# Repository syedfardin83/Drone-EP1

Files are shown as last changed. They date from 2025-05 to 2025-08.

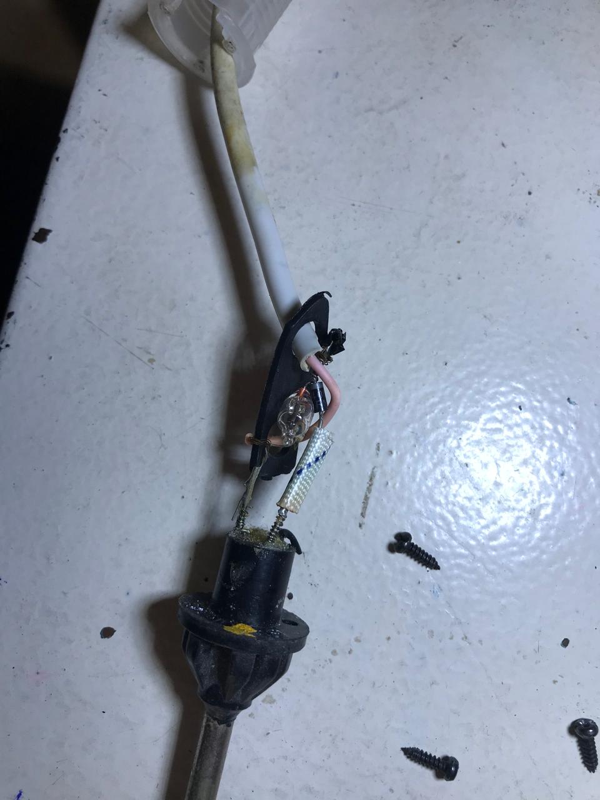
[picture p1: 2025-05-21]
Images/solder gun.jpg

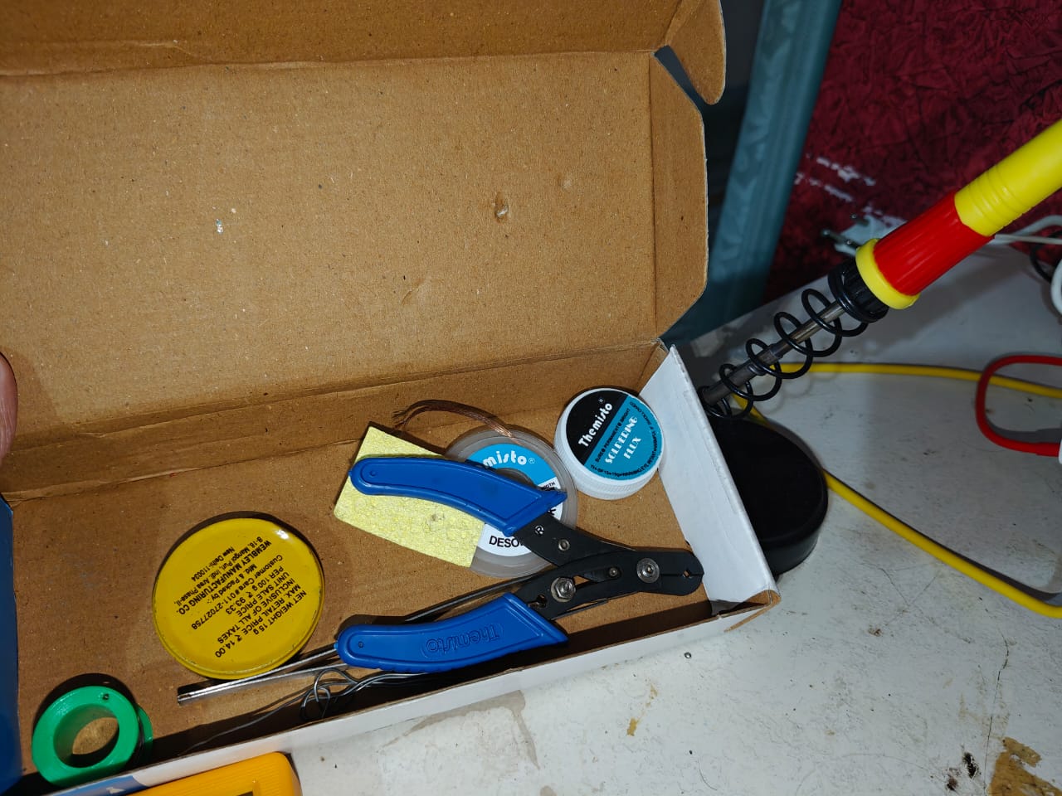
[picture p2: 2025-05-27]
Images/Soldering set.jpg

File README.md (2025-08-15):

##  LOS (Lark OS):
LOS is a firmware specifically built for the drone flight controller Lark1.

It inludes:
- Reading desired angles/rates from the in-built bluetooth on the ESP32.
- Reading the IMU data (MPU6050).
- Using a complementary filter to obtain the current angles of the drone.
- A PID loop to maintain stability and a smooth flight.

### LOS 1.0
A super loop firmware, with only 1dof control (throttle coontrol only). It was built to test basic tasks like Bluetooth reading, commands string formatting, and motor PWM outputs. It does not include IMU reading and PID calculations.

It is tested and works well.

### LOS 1.1
It was supposed to be complete functional drone superloop firmware with 6dof. But, it did not function, due to some superloop firmware complications.

It is tested and does not work. Hence, moving on to LOS2 which will be FreeRTOS based.

### LOS 2.0
It is a FreeRTOS based complete drone firmware. It has two tasks.
- BT read task
- MPU read + PID calculation

As the Bluetooth task was in the same task in LOS1.1, it was causing the major lag, hence LOS2.0 separates the BT task, while the rest of the tasks are together in another task.

### LOS 2.1
It is an improverment over the LOS 2.0, which now includes 4 tasks.
- BT reading
- IMU reading
- Angles calculation - Complementary filter
- PID loop

LOS 2.1 is more robust, as it uses queues for intertransmission of data between tasks.

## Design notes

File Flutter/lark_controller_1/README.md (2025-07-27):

# lark_controller_1

A new Flutter project.

## Getting Started

This project is a starting point for a Flutter application.

A few resources to get you started if this is your first Flutter project:

- [Lab: Write your first Flutter app](https://docs.flutter.dev/get-started/codelab)
- [Cookbook: Useful Flutter samples](https://docs.flutter.dev/cookbook)

For help getting started with Flutter development, view the
[online documentation](https://docs.flutter.dev/), which offers tutorials,
samples, guidance on mobile development, and a full API reference.

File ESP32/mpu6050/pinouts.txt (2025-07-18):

MPU6050     ESP32

VCC	     3.3v
GND	     GND
SDA	     25
SCL	     26

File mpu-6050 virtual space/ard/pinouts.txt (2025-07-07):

MPU6050     Arduino Uno

VCC	     5V 
GND	     GND
SDA	     A4
SCL	     A5

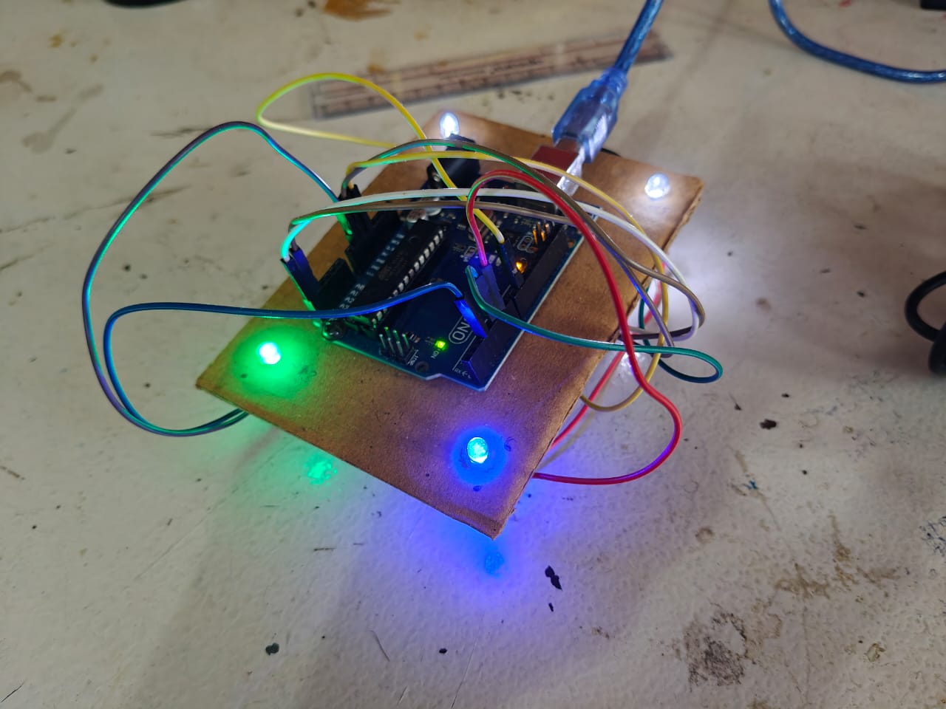
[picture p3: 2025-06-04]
Images/LED PID.jpeg

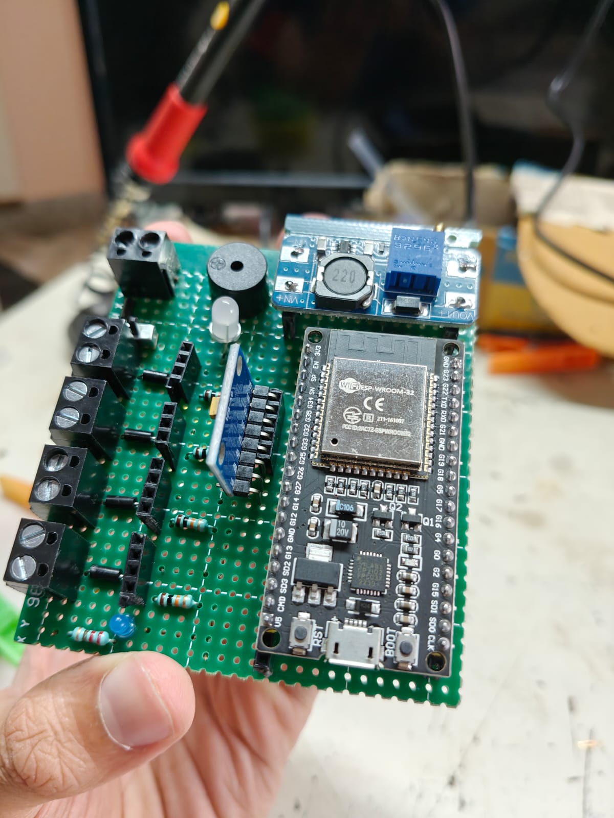
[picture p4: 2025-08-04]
Images/Lark1.jpeg

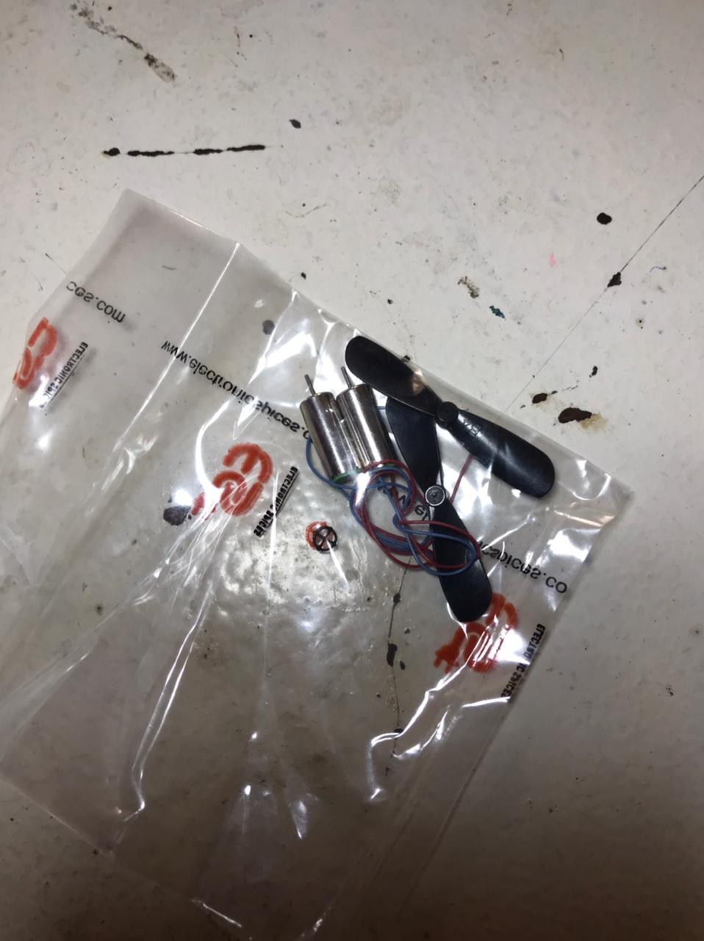
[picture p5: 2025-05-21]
Images/8520 Motors.jpg

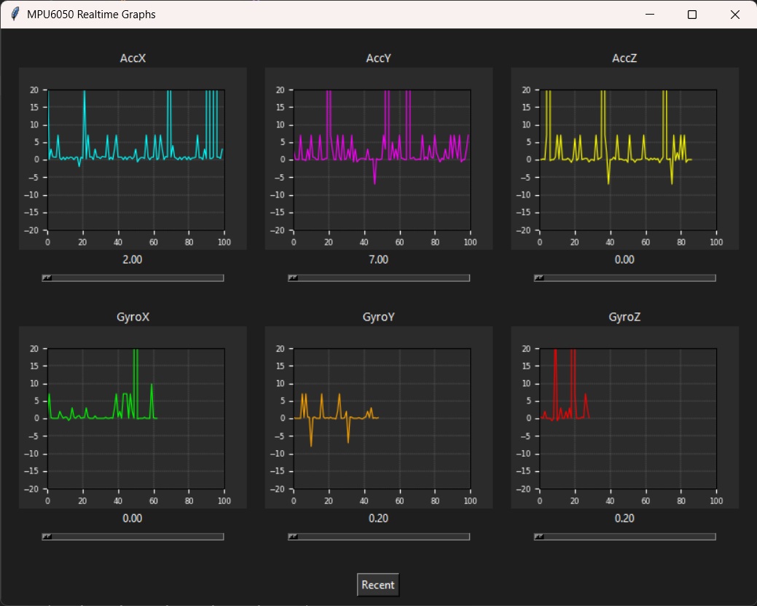
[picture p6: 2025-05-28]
Images/GUI 2.jpg

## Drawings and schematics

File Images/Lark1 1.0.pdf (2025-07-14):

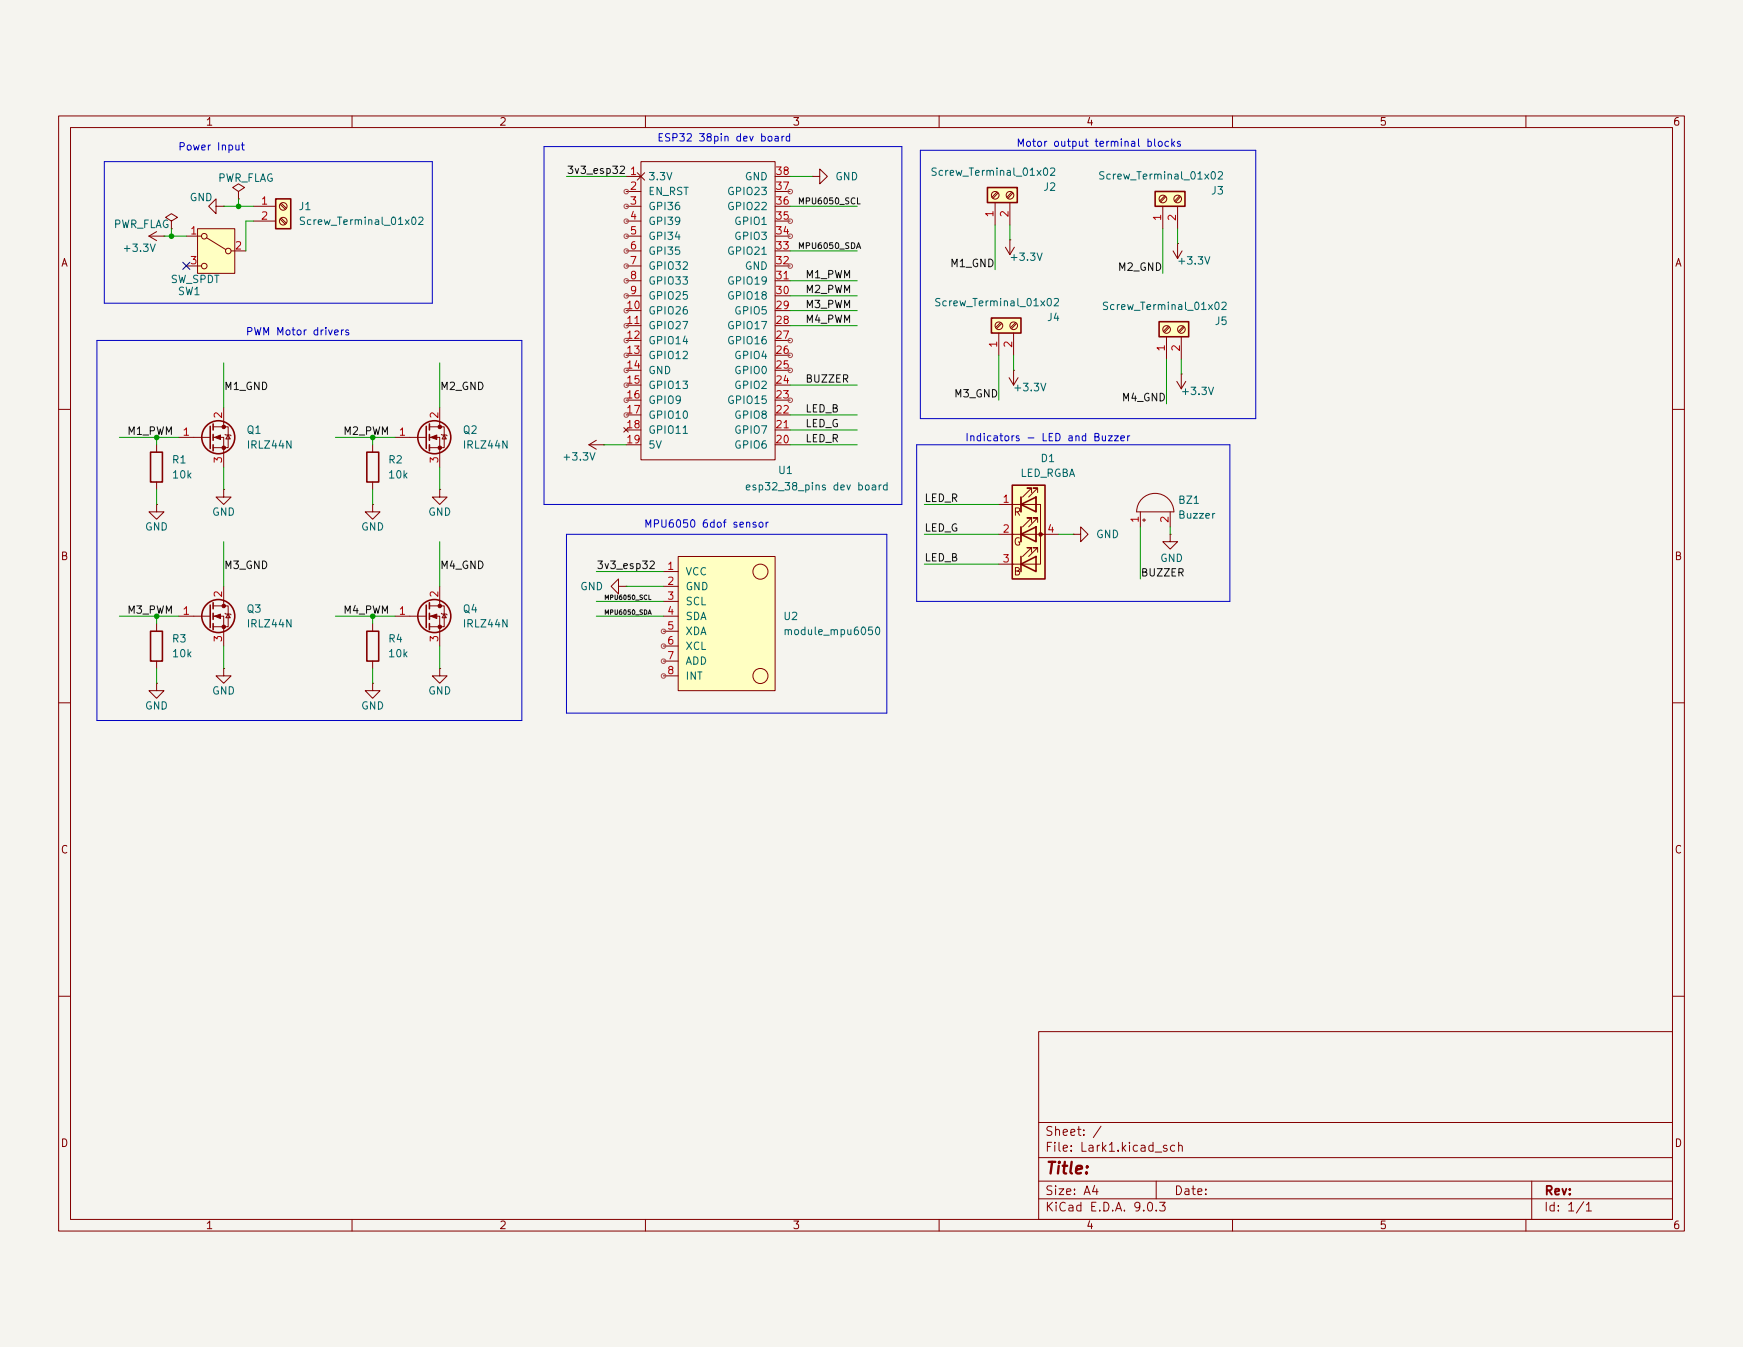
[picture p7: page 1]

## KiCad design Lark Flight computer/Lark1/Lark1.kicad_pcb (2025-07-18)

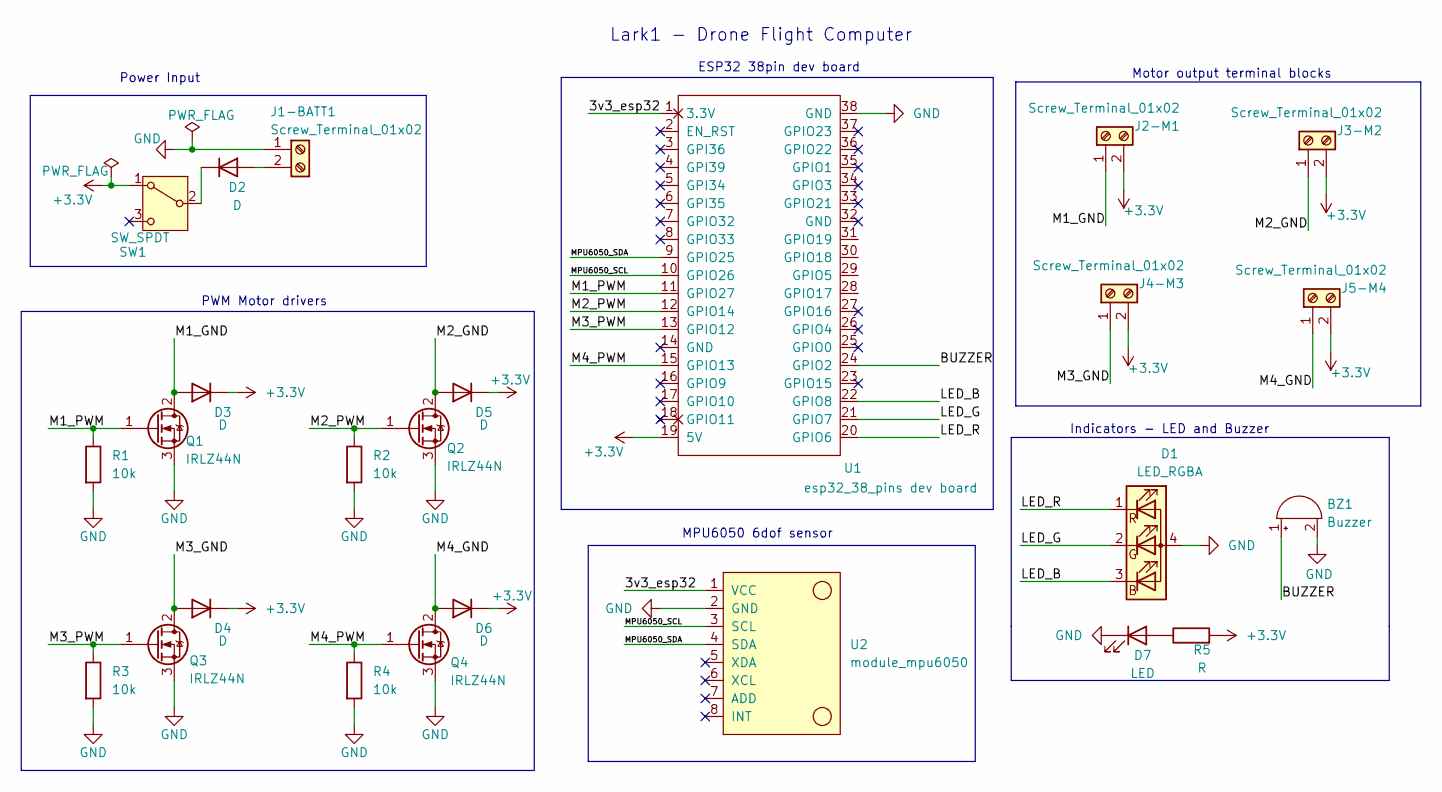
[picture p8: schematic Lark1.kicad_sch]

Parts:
BZ1: Buzzer; Buzzer_12x9.5RM7.6
D1: LED_RGBA; LED_D5.0mm-4_RGB_Wide_Pins
D2, D3, D4, D5, D6: D; D_5KPW_P12.70mm_Horizontal
D7: LED; LED_D3.0mm
J1-BATT1, J2-M1, J3-M2, J4-M3, J5-M4: Screw_Terminal_01x02; TerminalBlock_Altech_AK300-2_P5.00mm
Q1, Q2, Q3, Q4: IRLZ44N; TO-220-3_Vertical
R1, R2, R3, R4: 10k; R_Axial_DIN0204_L3.6mm_D1.6mm_P5.08mm_Horizontal
R5: R; R_Axial_DIN0204_L3.6mm_D1.6mm_P5.08mm_Horizontal
SW1: SW_SPDT; SW_Slide_SPDT_Angled_CK_OS102011MA1Q
U1: esp32_38_pins dev board; PinSocket_2x19_P2.54mm_Vertical
U2: module_mpu6050; PinSocket_1x08_P2.54mm_Vertical

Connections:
+3.3V: D3.1 (K), D4.1 (K), D5.1 (K), D6.1 (K), J2-M1.2, J3-M2.2, J4-M3.2, J5-M4.2, R5.2, SW1.1 (A), U1.19 (5V)
/3v3_esp32: U1.1 (3.3V), U2.1 (VCC)
/BUZZER: BZ1.1 (+), U1.24 (GPIO2)
/LED_B: D1.3 (BK), U1.22 (GPIO8)
/LED_G: D1.2 (GK), U1.21 (GPIO7)
/LED_R: D1.1 (RK), U1.20 (GPIO6)
/M1_GND: D3.2 (A), J2-M1.1, Q1.2 (D)
/M1_PWM: Q1.1 (G), R1.1, U1.11 (GPIO27)
/M2_GND: D5.2 (A), J3-M2.1, Q2.2 (D)
/M2_PWM: Q2.1 (G), R2.1, U1.12 (GPIO14)
/M3_GND: D4.2 (A), J4-M3.1, Q3.2 (D)
/M3_PWM: Q3.1 (G), R3.1, U1.13 (GPIO12)
/M4_GND: D6.2 (A), J5-M4.1, Q4.2 (D)
/M4_PWM: Q4.1 (G), R4.1, U1.15 (GPIO13)
/MPU6050_SCL: U1.10 (GPIO26), U2.3 (SCL)
/MPU6050_SDA: U1.9 (GPIO25), U2.4 (SDA)
GND: BZ1.2 (-), D1.4 (A), D7.1 (K), J1-BATT1.1, Q1.3 (S), Q2.3 (S), Q3.3 (S), Q4.3 (S), R1.2, R2.2, R3.2, R4.2, U1.38 (GND), U2.2 (GND)
unnamed: D2.2 (A), J1-BATT1.2
unnamed: D2.1 (K), SW1.2 (B)
unnamed: D7.2 (A), R5.1

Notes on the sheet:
Indicators - LED and Buzzer
PWM Motor drivers
Power Input
MPU6050 6dof sensor
Lark1 - Drone Flight Computer
ESP32 38pin dev board
Motor output terminal blocks

Board: 2 copper layers, 25 parts (0 on the bottom side), 20 nets, no tracks yet.

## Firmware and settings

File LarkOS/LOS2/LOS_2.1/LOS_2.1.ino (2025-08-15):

//LOS 2.0 - FreeRTOS Based 6dof, bluetooth controlled Lark Firmware
//Three main tasks
//1. Bluetooth Input
//2. MPU6050 Sensor input and processing
//3. PID

//  Axis mapping:
//  x-axis : yaw
//  y-axis : pitch
//  z-axis : roll 

//ToDO:
//vTaskDelay after every task
//Proper heap memory allocation for each task

//  Importing modules
#include "BluetoothSerial.h"
#include <math.h>
#include <Adafruit_MPU6050.h>
#include <Adafruit_Sensor.h>
#include <Wire.h>

//  Defining App CPU  
#if CONFIG_FREERTOS_UNICORE
static const int app_cpu = 0;
#else
static const int app_cpu = 1;
#endif

//  Software Objects
BluetoothSerial SerialBT;
Adafruit_MPU6050 mpu;

//  BT read variables
String inputString = "";
bool stringEnd = false;
char ch;

// Drone control variables
double desiredAngles[3] = {0,0,0}; ////////////////////////////
double throttleIncrement = 0;
double throttle = 0; //////////////////
double* offsets;
double integratedAngles[3] = {0,0,0};
double accAngles[3] = {0,0,0};
double compAngles[3] = {0,0,0};
double alpha = 0.98;

//MPU
#define SCL_PIN 17
#define SDA_PIN 26
double* mpu_data;////////////////////////////

// PID variables
double P=0.09,I=0.01,D=0.01;
double P_terms[3] = {0,0,0};
double I_terms[3] = {0,0,0};
double D_terms[3] = {0,0,0};
double current_errors[3] = {0,0,0};
double previous_errors[3] = {0,0,0};
double rate_outputs[3] = {0,0,0};

// Motor inputs
int motor_inputs[4] = {0,0,0,0};

// Time variables
double dt1;

#define bt_name "LOS 2.0"

//  FreeRTOS Queues
static QueueHandle_t desiredAnglesQ;
static uint8_t desiredAnglesQ_l = 3;

static QueueHandle_t throttleQ;
static uint8_t throttleQ_l = 3;

static QueueHandle_t mpu_dataQ;
static uint8_t mpu_dataQ_l = 3;

static QueueHandle_t dt1Q;
static uint8_t dt1Q_l = 3;

static QueueHandle_t current_anglesQ;
static uint8_t current_anglesQ_l = 3;


String* splitBySpace(String str){
  static String words[10];int i=0;String word = "";int wordIndex = 0;
  while(i<str.length()){
    if((str[i]==' ')){
      words[wordIndex] = word;
      word="";
      wordIndex++;i++;
      continue;
    }
    if(i==str.length()-1){
      word+=str[i];
      words[wordIndex] = word;break;
    }
    word+=str[i];
    i++;
  }
  return words;
}

double* getData(){
  /* Get new sensor events with the readings */
  sensors_event_t a, g, temp;
  mpu.getEvent(&a, &g, &temp);
  static double arr[6];
  arr[0] = a.acceleration.x;
  arr[1] = a.acceleration.y;
  arr[2] = a.acceleration.z;

  arr[3] = g.gyro.x;
  arr[4] = g.gyro.y;
  arr[5] = g.gyro.z;
  return arr;
  // AccX = a.acceleration.x
  // return [a.acceleration.x,a.acceleration.y,a.acceleration.z,a.gyro.x,a.gyro.y,a.gyro.z];
  // double data[6] = {a.acceleration.x, a.acceleration.y, a.acceleration.z, a.gyro.x, a.gyro.y, a.gyro.z};
}

double* getFilteredData(int n){
  double sums[6] = {0,0,0,0,0,0};

  static double avgs[6];

  //Finding sums
  for(int i=1; i<=n; i++){
    static double* data;
    data = getData();
    for(int j=0; j<6; j++){
      sums[j] = sums[j]+data[j];
    }
  }

  //Finding avgs
  for(int i=0; i<6; i++){
    avgs[i] = sums[i]/n;
  }

  return avgs;
}

double* calliberateSensor(){
  static double offsets[6];
  static double* data;
  data = getFilteredData(5);

  for(int i=0; i<6; i++){
    offsets[i] = data[i];
  }

  return offsets;
}

//  FreeRTOS Tasks
void BT_update_task(void *param){
  Serial.println("Entered the bluetooth task");
  int i;
  while(1){
    if(SerialBT.available()){
      ch = SerialBT.read();
      if(ch=='\n'){
        stringEnd = true;
        inputString.trim();
      }else{
        inputString+=ch;
      }
    }
    if(stringEnd){
      String* commands = splitBySpace(inputString);

      //Update desired angles
      for(i=0;i<3;i++){
        desiredAngles[i] = radians(commands[i].toDouble());
      }
      throttleIncrement = commands[3].toDouble();
      throttle+=(throttleIncrement*0.1);
      throttleIncrement = 0;

      //  Push to queue
      if(xQueueSend(desiredAnglesQ, desiredAngles,3) != pdTRUE){
        Serial.println("desiredAnglesQ full!");
      }

      if(xQueueSend(throttleQ, &throttle, 3) != pdTRUE){
        Serial.println("throttle Q full!");
      }

      inputString = "";
      stringEnd = false;
    }
    vTaskDelay(10/portTICK_PERIOD_MS);
  }
}

void mpu_read_pid_task(void *param){
  Serial.println("Entered MPU task");
  static TickType_t last_tick;
  static TickType_t curr_tick;
  int i;

  while(1){
    // prev_tick = xTaskGetTickCount();
    last_tick = xTaskGetTickCount();
    mpu_data = getFilteredData(5);
    curr_tick = xTaskGetTickCount();

    dt1 = ((curr_tick-last_tick)*portTICK_PERIOD_MS)/1000;
    
    //  Push To Queue
    if(xQueueSend(mpu_dataQ, mpu_data, 3) != pdTRUE){
      Serial.println("mpu_dataQ full!");
    }

    if(xQueueSend(dt1Q, &dt1, 3) != pdTRUE){
      Serial.println("dt1Q full!");
    }

    vTaskDelayUntil(&last_tick, 40/portTICK_PERIOD_MS);
  }
}

void calculate_angles_task(void *param){
  double dt1; double mpu_data_local[6];int i;
  while(1){
    //  Read Queues
    if(xQueueReceive(dt1Q,&dt1,3)!=pdTRUE){
      Serial.println("Failed to read dt1Q");
    }
    
    if(xQueueReceive(mpu_dataQ,&mpu_data_local,3) != pdTRUE){
      Serial.println("Failed to read mpu_dataQ");
    }

    //  Integrate Angles
    for(i=0;i<3;i++){
      integratedAngles[i]+=dt1*(mpu_data_local[i+3]-offsets[i+3]);
    }

    //  Acc angles
    accAngles[0] = -integratedAngles[0];
    if(mpu_data[0]==0){
      accAngles[1] = 3.14/2;
      accAngles[2] = 3.14/2;     
    }else{
      accAngles[1] = atan(mpu_data_local[2]/mpu_data_local[0]);
      accAngles[2] = atan(mpu_data_local[1]/mpu_data_local[0]);
    }

    //  Complementary filter
    for(i=0;i<3;i++){
      compAngles[i] = alpha*integratedAngles[i] + (1-alpha)*accAngles[i];
    }

    //  Update Queue
    if(xQueueSend(current_anglesQ,&compAngles,3)!=pdTRUE){
      Serial.println("current_anglesQ full!");
    }
  }
}

void pid_task(void *param){
  double current_angles[3]; double desired_angles_loacal[3]; double throttle_local;
  static TickType_t last_tick;
  static TickType_t curr_tick;
  double dt2;
  while(1){
    //  Read Queues
    if(xQueueReceive(current_anglesQ,&current_angles,3)!=pdTRUE){
      Serial.println("Failed to read current_anglesQ");
    }

    if(xQueueReceive(desiredAnglesQ,&desired_angles_loacal,3)!=pdTRUE){
      Serial.println("Failed to read desiredAnglesQ");
    }

    if(xQueueReceive(throttleQ,&throttle_local,3)!=pdTRUE){
      Serial.println("Failed to read throttleQ");
    }

    //Find errors
    prev_tick = xTaskGetTickCount();
    for(i=0;i<3;i++){
      current_errors[i] = current_angles[i]-desired_angles_loacal[i];
    }
    curr_tick = xTaskGetTickCount();
    dt2 = ((curr_tick-last_tick)*portTICK_PERIOD_MS)/1000;


    //Find rate outputs
    //****************** dt not properly calculated *****************************
    for(i=0;i<3;i++){
      P_terms[i] = P*current_errors[i];
      I_terms[i] = I_terms[i]+I*current_errors[i]*dt2;
      D_terms[i] = (current_errors[i]-previous_errors[i])/dt2;

      rate_outputs[i] = P_terms[i];
    }
    
    motor_inputs[0] = (throttle_local+rate_outputs[1]-rate_outputs[2]+rate_outputs[0])*255;
    motor_inputs[1] = (throttle_local+rate_outputs[1]+rate_outputs[2]-rate_outputs[0])*255;
    motor_inputs[2] = (throttle_local-rate_outputs[1]+rate_outputs[2]+rate_outputs[0])*255;
    motor_inputs[3] = (throttle_local-rate_outputs[1]-rate_outputs[2]-rate_outputs[0])*255;

    // **************** Give motor inputs - waiting ****************************
  }
}

void setup() {
  SerialBT.begin(bt_name);
  Serial.begin(115200);
  delay(100);

  //  Intitialize FreeRTOS Queues
  desiredAnglesQ = xQueueCreate(desiredAnglesQ_l, sizeof(double)*3);
  throttleQ = xQueueCreate(throttleQ_l, sizeof(double));
  mpu_dataQ = xQueueCreate(mpu_dataQ_l, sizeof(double)*6);
  dt1Q = xQueueCreate(dt1Q_l, sizeof(double));
  current_anglesQ = xQueueCreate(current_anglesQ_l, sizeof(double)*3);

  //  Initialize MPU6050
  Wire.begin(SDA_PIN,SCL_PIN);
  if (!mpu.begin()) {
    Serial.println("Failed to find MPU6050 chip");
    while (1) {
      delay(10);
    }
  }
  mpu.setAccelerometerRange(MPU6050_RANGE_16_G);
  mpu.setGyroRange(MPU6050_RANGE_250_DEG);
  mpu.setFilterBandwidth(MPU6050_BAND_21_HZ);
  delay(100);

  //Calliberate sensor
  offsets = calliberateSensor();

    //Create and run MPU task
  xTaskCreatePinnedToCore(
    mpu_read_pid_task,
    "mpu_read_pid_task",
    2048,
    NULL,
    1,
    NULL,
    app_cpu
  );
  delay(100);
  //Create and run BT task
  xTaskCreatePinnedToCore(
    BT_update_task,
    "Bluetooth read and update",
    2048,
    NULL,
    1,
    NULL,
    app_cpu
  );
  //Create and run Calculate Angles task
  xTaskCreatePinnedToCore(
    calculate_angles_task,
    "Calculate Angles",
    2048,
    NULL,
    2,
    NULL,
    app_cpu
  );
  //Create and run PID task
  xTaskCreatePinnedToCore(
    pid_task,
    "PID",
    2048,
    NULL,
    2,
    NULL,
    app_cpu
  );

}

void loop() {
}

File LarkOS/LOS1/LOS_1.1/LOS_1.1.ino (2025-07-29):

//Lark OS 1.1
// six degrees of freedom (input from joystick)
// Main tasks:
// 1. Take bluetooth input
// 2. Read sensor data
// 3. Run PID

#include "BluetoothSerial.h"
#include <Arduino.h>
#include <Adafruit_MPU6050.h>
#include <Adafruit_Sensor.h>
#include <Wire.h>
#include <math.h>

// Software Objects
BluetoothSerial SerialBT;
Adafruit_MPU6050 mpu;

// Motor pins
int motor_pins[4] = {12,13,14,27};

// Sensor orientation
#define orientation 2

// Indicator Pins
#define LED_R_PIN NULL
#define LED_G_PIN 22
#define LED_B_PIN 23
#define BUZZER_PIN NULL

// MPU6050 pins
#define SCL_PIN 17
#define SDA_PIN 26

// Test button
#define BTN_PIN NULL

// Bluetooth name
#define bt_name "LOS 1.1"

// Serial reading variables
String inputString = "";
bool stringEnd = false;

// Drone control variables
double desiredAngles[3] = {0,0,0};
double throttleIncrement = 0;
double throttle = 0;
double currentAngles[3] = {0,0,0};
double* offsets;
double* data;
double integratedAngles[3] = {0,0,0};
double accAngles[3] = {0,0,0};
double alpha = 0.98;

// Time variables
unsigned long previous_time = 0;
unsigned long current_time = 0;
double dt;

// PID variables
double P=0.09,I=0.01,D=0.01;
double P_terms[3] = {0,0,0};
double I_terms[3] = {0,0,0};
double D_terms[3] = {0,0,0};
double current_errors[3] = {0,0,0};
double previous_errors[3] = {0,0,0};
double rate_outputs[3] = {0,0,0};

// Motor inputs
int motor_inputs[4] = {0,0,0,0};

double* getData(){
  /* Get new sensor events with the readings */
  sensors_event_t a, g, temp;
  mpu.getEvent(&a, &g, &temp);
  static double arr[6];
  arr[0] = a.acceleration.x;
  arr[1] = a.acceleration.y;
  arr[2] = a.acceleration.z;

  arr[3] = g.gyro.x;
  arr[4] = g.gyro.y;
  arr[5] = g.gyro.z;
  return arr;
  // AccX = a.acceleration.x
  // return [a.acceleration.x,a.acceleration.y,a.acceleration.z,a.gyro.x,a.gyro.y,a.gyro.z];
  // double data[6] = {a.acceleration.x, a.acceleration.y, a.acceleration.z, a.gyro.x, a.gyro.y, a.gyro.z};
}

double* getFilteredData(int n){
  double sums[6] = {0,0,0,0,0,0};

  static double avgs[6];

  //Finding sums
  for(int i=1; i<=n; i++){
    static double* data;
    data = getData();
    for(int j=0; j<6; j++){
      sums[j] = sums[j]+data[j];
    }
  }

  //Finding avgs
  for(int i=0; i<6; i++){
    avgs[i] = sums[i]/n;
  }

  return avgs;
}

double* calliberateSensor(){
  static double offsets[6];
  static double* data;
  data = getFilteredData(5);

  for(int i=0; i<6; i++){
    offsets[i] = data[i];
  }

  return offsets;
}

String* splitBySpace(String str){
  static String words[10];int i=0;String word = "";int wordIndex = 0;
  while(i<str.length()){
    if((str[i]==' ')){
      words[wordIndex] = word;
      word="";
      wordIndex++;i++;
      continue;
    }
    if(i==str.length()-1){
      word+=str[i];
      words[wordIndex] = word;break;
    }
    word+=str[i];
    i++;
  }
  return words;
}

void setup() {
  //Initialize all pins
  for(int i=0;i<4;i++){
    pinMode(motor_pins[i],OUTPUT);
  }

  // pinMode(LED_R_PIN,OUTPUT);
  pinMode(LED_G_PIN,OUTPUT);
  pinMode(LED_B_PIN,OUTPUT);
  pinMode(BUZZER_PIN,OUTPUT);

  pinMode(BTN_PIN,INPUT);

  //Initialize Serial
  SerialBT.begin(bt_name);
  Serial.begin(115200);
  delay(100);

  //Initialize MPU6050
  Wire.begin(SDA_PIN,SCL_PIN);
  if (!mpu.begin()) {
    Serial.println("Failed to find MPU6050 chip");
    while (1) {
      delay(10);
    }
  }
  mpu.setAccelerometerRange(MPU6050_RANGE_16_G);
  mpu.setGyroRange(MPU6050_RANGE_250_DEG);
  mpu.setFilterBandwidth(MPU6050_BAND_21_HZ);
  delay(100);

  //Calliberate sensor
  offsets = calliberateSensor();
}

void loop() {

  //Bluetooth read
  if(SerialBT.available()){
    char ch = SerialBT.read();
    if (ch == '\n') {
      stringEnd = true;
    } else {
      inputString += ch;
    }
  }
  if(stringEnd){
        inputString.trim();
        if(inputString=="STOP"){
          Serial.println("Emergency stop protocol initiated !!!");
          for(int i=0;i<4;i++){
            analogWrite(motor_pins[i],0);
          }
          while(1){

          }
        }
        Serial.println(inputString);
        String* command = splitBySpace(inputString);

        //Update desired angles
        for(int i=0;i<3;i++){
          desiredAngles[i] = radians(command[i].toDouble());
        }
        throttleIncrement = command[3].toDouble();
        throttle+=throttleIncrement;
        throttleIncrement = 0;

        inputString = "";
        stringEnd = false;

        // Serial.print(throttle);
        // Serial.print("  ");
        // for(int i=0;i<3;i++){
        //   Serial.print(desiredAngles[i]);
        //   Serial.print("  ");
        }
        // Serial.println("");


  // Read Sensor data
    // current_time = micros();
    // data = getFilteredData(5);


    // // Calculate angles
    // dt = (current_time-previous_time)*pow(10,-6);
    // //Integrated Angles
    // for(int i=0;i<3;i++){
    //   integratedAngles[i]+=dt*(data[i+3]-offsets[i+3]);
    // }

    // //Angles from triginometry/Acceletration
    // if(orientation == 2){
    //   if(data[0]==0){
    //     accAngles[1] = 3.14/2;
    //     accAngles[2] = 3.14/2;
    //   }else{
    //         accAngles[2] = atan(data[1]/data[0]);
    //         accAngles[1] = atan(data[2]/data[0]);
    //   }
    // }
    // //Sign correction
    // if(orientation==2){
    //   // double temp=integratedAngles[0];
    //   accAngles[2] = -accAngles[2];
    //   // integratedAngles[0] = -temp;
    // }
    // // accAngles[0] = integratedAngles[0];
    // // //Complementary filter
    // for(int i=1; i<3; i++){
    //   currentAngles[i] = alpha*integratedAngles[i] + (1-alpha)*accAngles[i];
    // }
    // currentAngles[0] = integratedAngles[0];

    // // PID control


    // // Finding errors in angles
    // for(int i =0;i<3;i++){
    //   current_errors[i] = currentAngles[i]-desiredAngles[i];
    // }

    // // // Find rate outputs:
    // for(int i=0;i<3;i++){
    //   P_terms[i] = P*current_errors[i];
    //   I_terms[i] = I_terms[i]+I*current_errors[i]*dt;
    //   D_terms[i] = (current_errors[i]-previous_errors[i])/dt;

    //   rate_outputs[i] = P_terms[i];
    // }
    // //calculate motor inputs
    // motor_inputs[0] = (throttle-rate_outputs[0]-rate_outputs[1]+rate_outputs[2])*255;
    // motor_inputs[1] = (throttle-rate_outputs[0]+rate_outputs[1]-rate_outputs[2])*255;
    // motor_inputs[2] = (throttle+rate_outputs[0]+rate_outputs[1]+rate_outputs[2])*255;
    // motor_inputs[3] = (throttle+rate_outputs[0]-rate_outputs[1]-rate_outputs[2])*255;

    // //Give motor inputs
    // for(int i=0;i<4;i++){
    //   if(motor_inputs[i]<0){
    //     motor_inputs[i] = 0;
    //   }
    //   else if(motor_inputs[i]>255){
    //     motor_inputs[i] = 255;
    //   }
    // }

    // for(int i=0;i<3;i++){

    //   previous_errors[i] = current_errors[i];
    // }
    // previous_time = current_time;
}

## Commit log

2025-05-27 mpu6050 mouse
    [2025-05-23 12;44;30;616541.csv, log1.csv]
2025-05-28 GUI 2 serial bug not fixed yet
    [GUI1.py, GUI2.py, bin.py]
2025-05-29 GUI 3 latency lowered - just created more threads.
2025-06-03 Acc method(in compFilter.py) and Gyro method(in virtualSpaceGyro.py) ready, next step is to combine them.
2025-06-03 tkVisualization of Pitch angle using acc and gyro, next step make complementary filter
2025-06-04 Started LED PID Coding
2025-06-05 Platform IO started and written basic Gyro code in c++
2025-06-06 PID coding done, P,I,D constants not found yet.
2025-06-06 video demonstration of led pid simulator
2025-06-13 Recorded values of PWM and MOSFET plus LED
2025-06-24 Motor driver done(Check images and videos)
    [arduino_led.csv]
2025-06-24 Motor driver Schematic in kicad done
    [motor_control.kicad_pcb, motor_control.kicad_sch]
2025-07-05 HC-05 finally works!!!!
    [motor_control.kicad_sch]
2025-07-07 PID Python UI done
2025-07-13 Lark1 Flight computer power input schematic kicad done
    [Lark1.kicad_pcb, Lark1.kicad_sch]
2025-07-14 ESP32 mpu6050
2025-07-14 Lark1 almost done, indicators left
    [Lark1.kicad_sch]
2025-07-14 Lark1 1.0
    [Lark1.kicad_sch]
2025-07-14 Lark1 1.0 Schematic pdf added
2025-07-14 Lark1 refining
    [Lark1.kicad_sch]
2025-07-14 Lark1 Kicad ERC check - no errors
    [Lark1.kicad_sch]
2025-07-18 LarkOS1 started
    [Lark1.kicad_pcb, Lark1.kicad_sch]
2025-07-18 Complementary filter in esp32
2025-07-19 LOS 1.1 DONE!! PID works fine.
2025-07-19 LOS 1.1 minor bug fixes
    [LOS_1.1.ino]
2025-07-19 LOS 1.1 z-axis rotation remaining, rest all is good. Next up, make drone body and BT transmission from laptop
2025-07-19 LOS 1.1 minor fixes
    [LOS_1.1.ino]
2025-07-19 LOS 1.1 Bug fixes
    [LOS_1.1.ino, xbox_transmitter.py]
2025-07-23 LARK1 motor pinouts
2025-07-26 LOS1 - thrust only control in ESP32/Bluetooth
2025-08-04 LOS2 - comp filter untested
2025-08-04 LOS2 PID - untested; LOS2 done?
2025-08-15 calculate_angles_task done; PID task - from calculating dt; ToDo pending;
